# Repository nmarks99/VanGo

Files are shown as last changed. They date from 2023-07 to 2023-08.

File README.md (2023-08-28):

# VanGo: A Drawing Robot
VanGo is a differential drive robot that can draw SVG images on a page.

<p float="left">
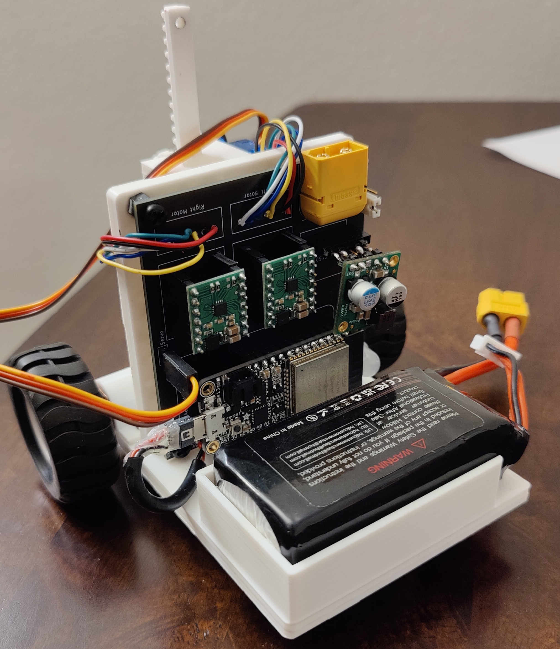
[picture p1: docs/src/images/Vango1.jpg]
  
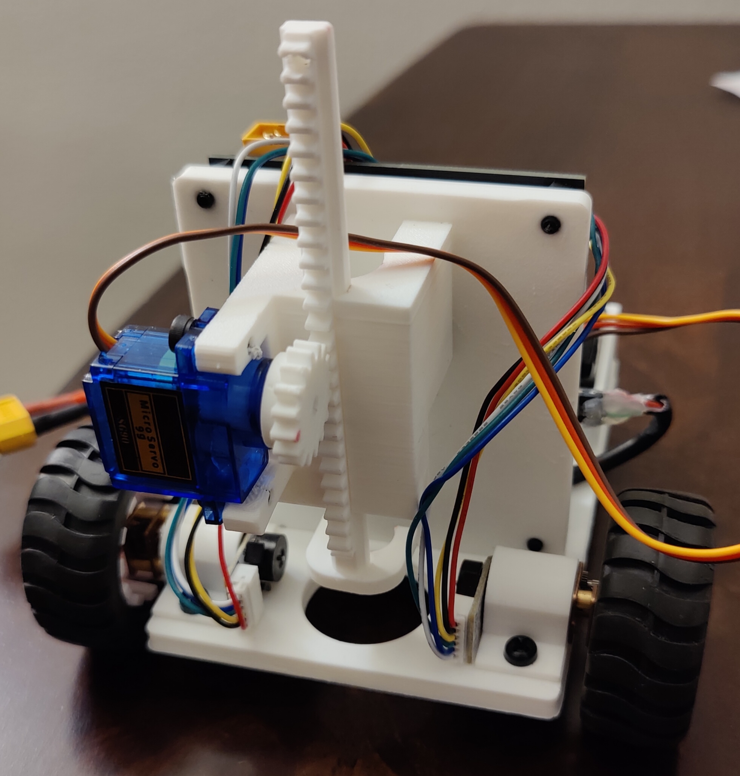
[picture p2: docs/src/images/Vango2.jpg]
   
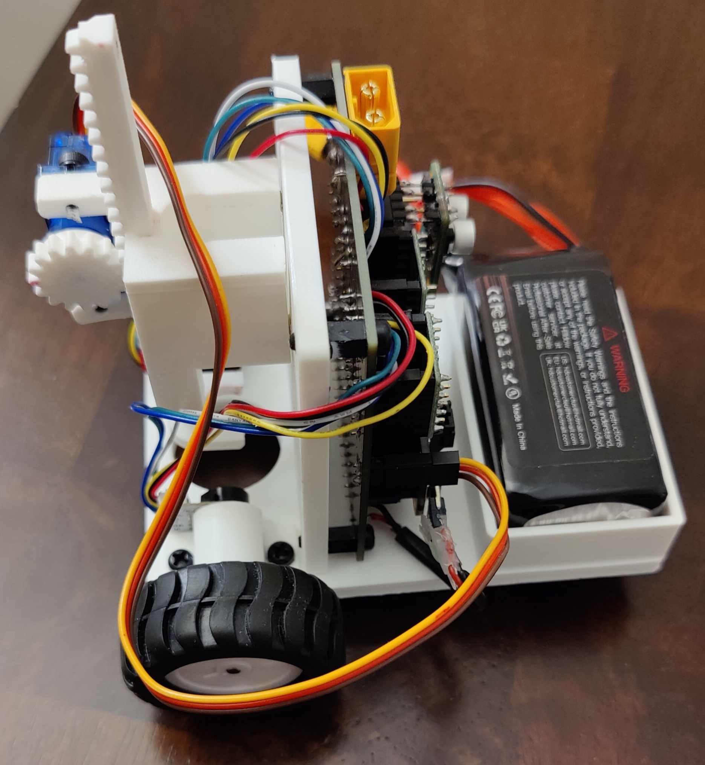
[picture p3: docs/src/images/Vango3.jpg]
  
</p>

First, an SVG image is converted to XY coordinates using this online tool: [Coordinator](https://spotify.github.io/coordinator/).
Then, using these XY coordinates, a trajectory of waypoints is generated for the robot to follow.
Trajectory tracking is implemented using a simple PID steering control algorithm, and the robot determines its pose in space
through wheel odometry, using quadrature encoders on the motors. For more in-depth information, please see the VanGo documentation
at [https://nmarks99.github.io/VanGo/](https://nmarks99.github.io/VanGo/). VanGo is still relatively early in development
and several aspects of the project need more work and fine tuning, such as the trajectory tracking algorithm, a command line interface
for the client application, and improved mechanical design. However, in its current state, VanGo demonstrates a good proof of concept.

## Project Structure
- `vango-firmware` is the firmware for the ESP32 board based on [esp-idf-hal](https://github.com/esp-rs/esp-idf-hal)
- `vango-client` is a desktop command line application for controlling the robot
- `vango-utils` is a utility library used by both the firmware and client.
- `hardware` directory contains the KiCAD project for the PCB

## Future Development
This project also uses another library I have developed, [diff-drive](https://github.com/nmarks99/diff-drive),
primarily for pose estimation via wheel odometry. In the future I hope to use both the VanGo and diff-drive projects
as starting points for developing a general purpose, high-performance, and open-source, differential drive robot
that anyone can build with firmware based on Rust on the ESP32 (think DIY [TurtleBot](https://www.robotis.us/turtlebot-3/)).

## Other Notes
One of my biggest motivations for this project was to learn more rust programming, particularly embedded rust, which is why
this project is 100% rust code 🦀. Like mostly everyone else, I've primarily used C and C++ for programming microcontrollers
in the past, most of the time using the Arduino framework together with PlatformIO which I've found to be a very pleasant
experience. After having worked on this project for several months, using Rust on the ESP32, I've found it to be a
equally pleasant experience, after some intial growing pains. Below are some of my opinions on the state of embedded Rust.
Note this is generally with regards to Rust on ESP [(esp-rs)](https://github.com/esp-rs), however some of it applies to embedded
Rust in a broader sense.

**The Good**
- Using `esp-idf-hal` you get to program the ESP32 in Rust (almost) as if you were writing a program on your desktop
This means you get to take full advantage of the Rust standard library and mostly any external crates you may need.
- Using Cargo works the same as it would in your other Rust projects and integrates seamlessly with flashing the board.
you can see in my vango-firmware/.cargo/config.toml file, I created an alias `cargo flash` to flash the board from the
command line and also set the partition table (sets how much space in memory you are reserving for your program):
`flash = "espflash --release --partition-table partitions.csv"`
- As in the case for non-embedded Rust, if the code compiles it almost always just works, which is super nice, especially
for embedded projects where you not only have to build, but also flash the board. I've found that bugs are often very easy
to track down in Rust. The only subtle error I encountered, and it's not even that subtle, is that if you accidentally
enter a loop that is doing nothing but looping, it will probably trigger the watchdog timer and continually reset the board.
There is a way to disable the WDT, but you can also just add a short delay (1ms even is enough) if you are in a loop doing
nothing.

**The Bad**
- Finding example code is (unsurpisingly since Arduino is much more mature) a little difficult compared to Arduino.
For example, I had a very tough time finding an example of how to do some basic things like GPIO interrpts
and timer based interrupts, which I could find examples for very easily in Arduino. However, after figuring it out,
a timer interrupt in `esp-idf-hal` turns out to be almost as easy to use as the popular [IntervalTimer](https://www.pjrc.com/teensy/td_timing_IntervalTimer.html)
in Arduino. Another thing that was very tough to find example code for was bluetooth. Eventually I found [esp32-nimble](https://github.com/taks/esp32-nimble)
which works quite well and isn't too complicated. The developer is was also quick to reply to an issue I opened for an additional feature.
- Flashing the board takes *forever*. I haven't timed it but it probably takes like a minute or two maybe which is much longer than similar Arduino
programs. This may just be something specific to my project, but it was fairly annoying to wait for the board to be flashed whenever I made updates.

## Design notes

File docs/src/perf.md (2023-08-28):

# Performance
In its current stage, the VanGo drawing robot does not work well enough to draw
consistent and accurace images, however with additional tuning, a more sophisticated
trajectory tracking algorithm, and possibly additional sensors, the performance will
improve. Manual mode, which enables a user to manually drive the robot and move
the marker up and down works as desired. Below the results of several tests are shown.

## Test 1: Manual Mode "Hi"
In the video linked below, I manually controlled the robot using the `vango-client`
application to write "Hi". This worked fairly well, but as you can see, driving the robot
smoothly with the current controls is a bit challenging.

[Test 1 Video](https://drive.google.com/file/d/1G3J-nfXMaDWAlqaTBmTTMUwiaXZAd-wS/view?usp=sharing)

## Test 2: Automatic Mode "Triangle"
The video linked below performs a test of the robot in automatically mode
attempting to draw a triangle. There is also a plot of the estimated x and y
position of the robot from wheel odometry. As you can see the actual position
of the robot is not very good, however the position estimate from odometry appears to be
a bit better. This could potentially be due to wheel slipping.

[Test 2 Video](https://drive.google.com/file/d/1G4sDGH2qyjXhTE3TqAN95uGIOtFKYngA/view?usp=drive_link)

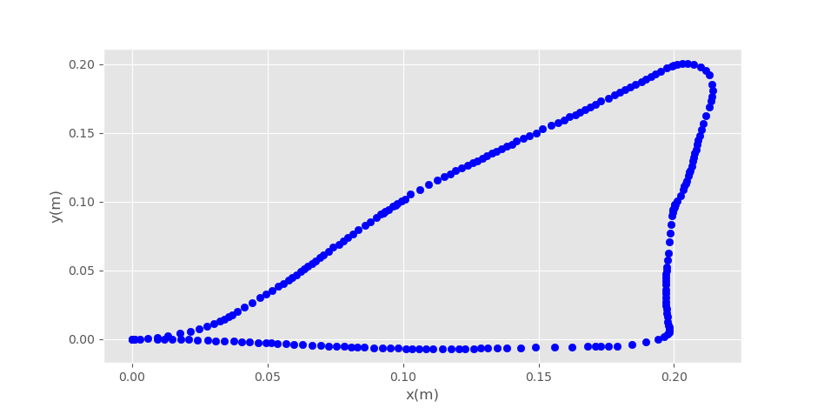
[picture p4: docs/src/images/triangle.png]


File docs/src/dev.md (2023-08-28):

# Embedded Development
To set up a development environment to modify and flash firmware to the device,
you will need to install several things such as the Espressif compiler toolchain,
espflash cargo utility, and of course rust and cargo if you don't have that already.

The best way to get all this setup and make sure it works is to follow the directions
on setting up an `esp-idf-template` project: [esp-idf-template](https://github.com/esp-rs/esp-idf-template).
If you are able to successfully build the template project, you should in theory be able to build and flash
the `vango-firmware` without issue. In the `vango-firmware/.cargo/config.toml` file, there is an alias
for "flash", which allows you to flash the board with `espflash` by simply typing `cargo flash`.

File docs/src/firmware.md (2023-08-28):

# Firmware
The firmware running on the ESP32 microcontroller is contained in the `vango-firmware` directory.
The firmware is responsible for establishing Bluetooth Low-Energy (BLE) communications,
reading encoders, computing wheel angles and speeds,and computing the robot's pose through wheel odometry.

## Communication
The VanGo robot is controlled via a BLE server. Using the `esp32-nimble` crate with `esp-idf-hal`,
several BLE characteristics are established. For those unfamiliar with BLE, a characteristic is simply
a part of the server that a client can read/write data to. Each characteristic is given a
unique UUID to identify it by.

Below are the BLE characteristics provided by the robot and some information about what they are for.

**Left/Right Speed Characteristics** (Read | Write):
- Read: When read from, returns the current wheel speed
- Write: When written to, sets the target wheel speed to the written value

**Pose X, Y, and \\(\theta\\) Characteristics** (Read | Write):
- Read: When read from, returns the current x,y, or \\(\theta\\) position of the robot
- Write: When '0' is written to these characteristics, the value is zeroed

**Pen Characteristic** (WRITE):
- Write: When '1' is written, raises the pen, when '0' is written, lowers the pen

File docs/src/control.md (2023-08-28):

# Control
VanGo's control architecture is comprised of a lower level speed control loop
and a higher level trajectory tracking controller. From a user perspective, the lower level
control loop can mostly be ignored, or at least treated as a black box and not modified, while the
higher level controller may leave more room for customization.

## Low-Level Speed Controller
Running on the ESP32 microcontroller, a timer based interrupt is resposible for reading the
quadrature wheel encoders to compute the speed of the wheels. Experimentally it was determined that
a simply proportional controller was sufficient for closed-loop speed control, although Proportional-Derivative (PD)
control was also tested. Although PD control results is a smoother trajectory with less overshoot, the slower response
was not worth the minimization of overshoot. Either way, both P and PD controllers work fairly well for closed-loop
speed control, and if one is preferred by the user, the gains may be adjusted in the firmware and reflashed to the board.
For more information on editing and flashing firmware, see [Development](./dev.md).

The two images below show the speed controller response for both the Proportional and Proportional-Derivative controllers.
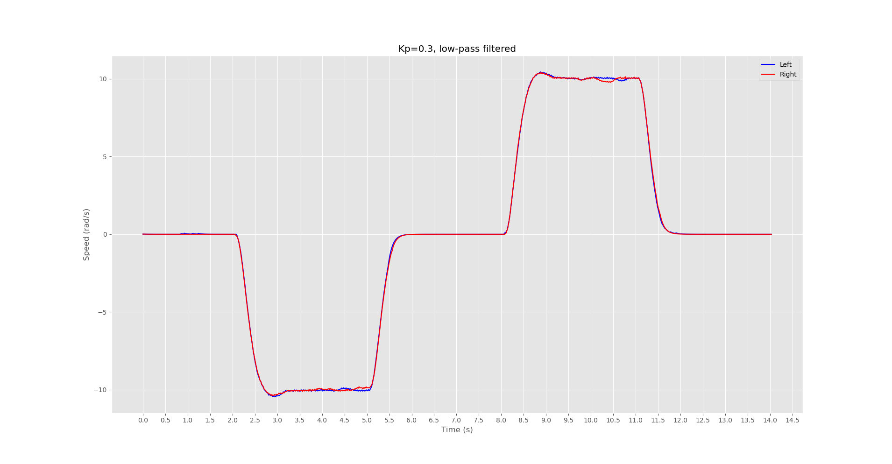
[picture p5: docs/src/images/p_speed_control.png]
Proportional control


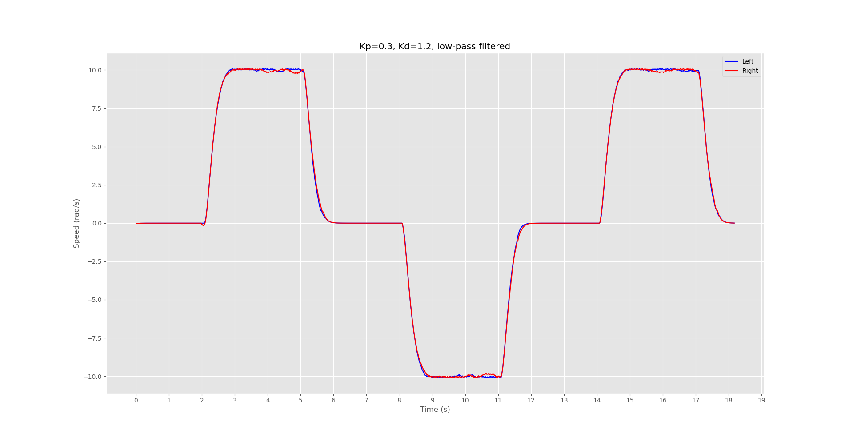
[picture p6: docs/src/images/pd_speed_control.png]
Proportional-Derivative control


## High-Level Trajectory Controller
The `vango-client` implements a trajectory tracking algorithm which is used to follow a trajectory defined
by a set of waypoints.

There are many different trajectory tracking algorithms in existance, however at this time only one,and perhaps the most basic one,the PID controller, has been implemented for the VanGo robot. There are various ways a PID controller can be applied to the trajectory tracking problem, however the method I've chosen to implement is to use a PID controller for angular velocity control. To move the robot from its current (x, y) to some goal position which is presumably along the target path, the algorithm works as follows:
1. Read the current pose (computed from wheel odometry) via BLE
2. Compute the target angle as \\(atan2(y_{goal} - y, x_{goal} - x)\\)
3. Let the error be the minimum angle between the robots current heading and the target heading
4. Compute the control signal from the PID controller for the given error. This control signal is chosen to represent the angular velocity of the robot.
5. The desired motion of the robot is then represented as a 2D twist (body velocity), using the computed target angular velocity, a constant x velocity of your choice, and a y velocity of 0.0 (which assumes no wheel slipping)
6. Compute the left and right wheel speeds needed to achieve the target twist

During development, there was a choice to be made regarding whether the trajectory controller
will operate at the client application level or the firmware level. Both options have positives and negatives and will be briefly discussed below. In the end, it was chosen to operate the trajectory controller at the client application level.

### Client-Side Trajectory Controller
A client side trajectory controller works by implementing the trajectory tracking algorithm in the `vango-client`
application. The controller will obtain the robots current pose using bluetooth low-energy (BLE) and compute the necessary wheel speeds for tracking the desired trajectory, and send those target wheel
speeds back to the robot over BLE.

**Pros**
- Faster development time since you will not need to reflash the microcontroller
- Easier to test different trajectory tracking algorithms or enable several algorithms to be available as options to the user
- Can take advantage of a client machine with higher computing power than the microcontroller

**Cons**
- Control loop speed is limited by BLE read/write latency. In it's current state, loop speeds top out around 30Hz.

### Firmware-Side Trajectory Controller
An alternative way to implement the trajectory tracking controller would be to implement the controller in the firmware on the microcontroller, obtaining the target path to follow from the client over BLE. Pros and Cons are listed below.

**Pros**
- The MCU is capable of more precise and consistant timing through the use of hardware timers and interrupts
- BLE communication latency is no longer a concern since waypoints could be sent and processed beforehand

**Cons**
- Resources are somewhat limited on the MCU and may impose practical limits of which algorithms can be employed
- Slower development time since for the most part, modifications to the trajectory tacking algorithm require reflashing the board

Although performance/timing of the control loop could potentially be better if implemented in the MCU, it was determined that easy customization of algorithms as well as development time are key aspects of the project, therefore a client-side trajectory tracking algorithm was employed.

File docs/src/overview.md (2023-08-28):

# Overview

<p float="left">
  
   
  
</p>

VanGo is a differential drive robot for drawing SVG images. Put simply,
VanGo is a wheeled mobile robot capable of trajectory tracking,
with the added feature that the trajectory is generated from an SVG
image and the robot holds a marker which is brought into contact with the
page while the robot is on the desired path, thus drawing the SVG image.

## Usage
A basic explanation of how VanGo is used and what goes on under-the-hood during general use is explained below.
More in-depth explaination can be found is later sections of this site.
1. The user produces a CSV file containing (x,y) points from a SVG image using [Coordinator](spotify.github.io/coordinator)
2. The user starts the `vango-client` program, providing the CSV file
3. A path of waypoints is generated from the CSV file and clustered into closed curves based on some threshold distance
4. The robot will navigate to the first point in the next closed curve
5. Lower the marker, then navigate to each additional point in the same closed curve
6. After passing through all the points in this closed curve, raise the marker and go back to step 4.

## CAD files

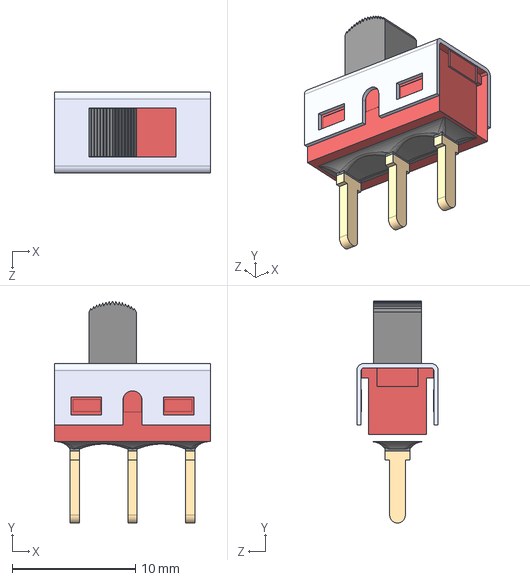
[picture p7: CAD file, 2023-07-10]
hardware/vango-pcb/500SSP1S1M2REA/500SSP1S1M2REA.step
12.7 x 18.0 x 6.60 mm

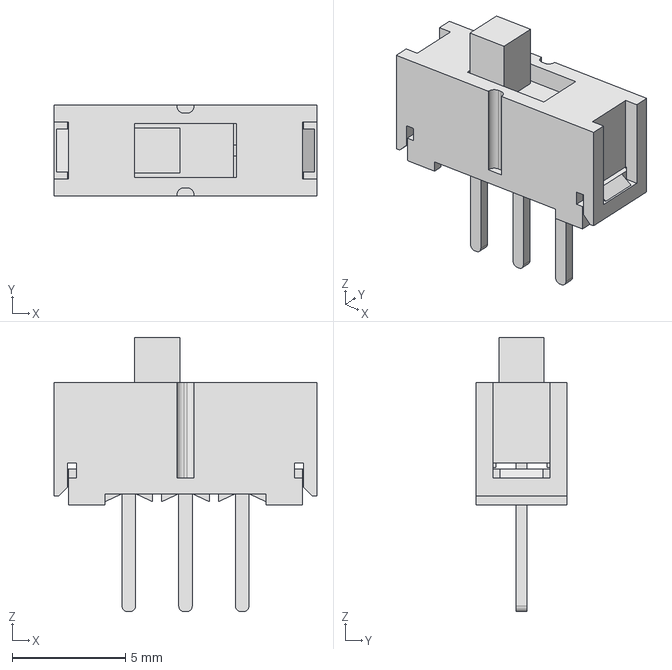
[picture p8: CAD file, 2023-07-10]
hardware/vango-pcb/EG1218_switch/EG1218.step
11.6 x 4.00 x 12.1 mm

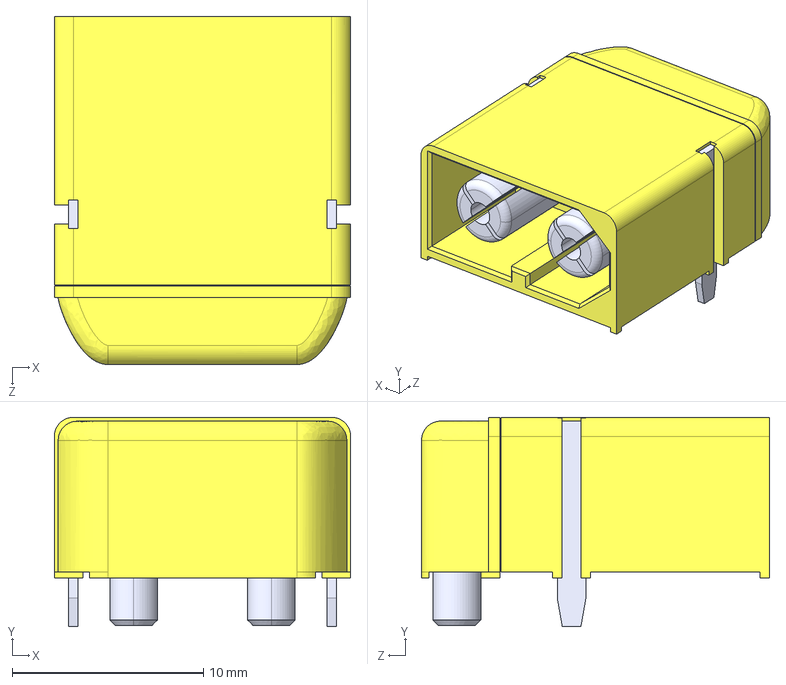
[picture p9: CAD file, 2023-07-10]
hardware/vango-pcb/XT60/XT60PW-M.step
15.5 x 11.0 x 18.2 mm

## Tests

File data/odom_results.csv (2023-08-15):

time(ms) | left_angle(rad) | right_angle(rad) | theta(rad) | x(m) | y(m)
25 | 0.00448799 | 0.00448799 | 0 | 0.00010097978 | 0
45 | 0.00448799 | 0.01795196 | 0.0029411586 | 0.00025244924 | 0.00000022178463
65 | 0.01795196 | 0.03141593 | 0.0029411586 | 0.00055538764 | 0.0000009642778
85 | 0.0448799 | 0.053855877 | 0.0019607726 | 0.001110775 | 0.0000021779802
105 | 0.07180784 | 0.080783814 | 0.0019607726 | 0.0017166525 | 0.0000033659696
125 | 0.107711755 | 0.11668773 | 0.0019607726 | 0.002524489 | 0.0000049499554
145 | 0.14810365 | 0.16605562 | 0.003921547 | 0.003534282 | 0.000007965572
165 | 0.20195954 | 0.22439949 | 0.00490193 | 0.0047965157 | 0.000013878634
185 | 0.2692794 | 0.2962073 | 0.0058823167 | 0.006361677 | 0.000022711372
205 | 0.3455752 | 0.36801517 | 0.00490193 | 0.008027817 | 0.00003209477
225 | 0.435335 | 0.45777494 | 0.00490193 | 0.010047388 | 0.000041994645
245 | 0.5340708 | 0.55651075 | 0.00490193 | 0.012268917 | 0.000052884512
265 | 0.63280654 | 0.6552465 | 0.00490193 | 0.014490445 | 0.00006377437
285 | 0.74051833 | 0.75847024 | 0.0039215307 | 0.016863443 | 0.000074841926
305 | 0.85720605 | 0.87067 | 0.0029411572 | 0.019438405 | 0.00008556373
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

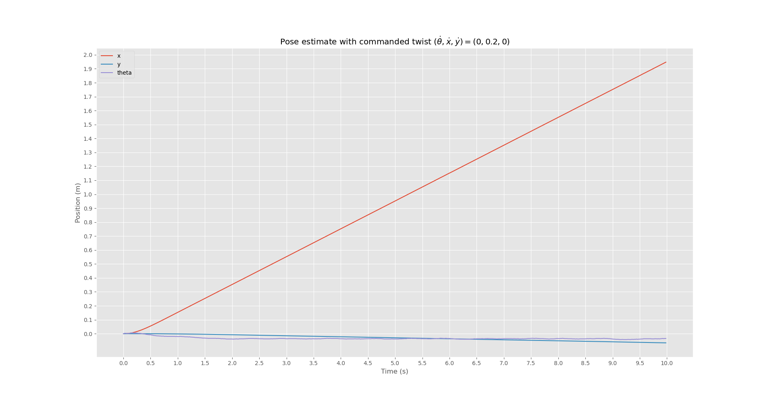
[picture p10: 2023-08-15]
docs/book/images/odom_results.png

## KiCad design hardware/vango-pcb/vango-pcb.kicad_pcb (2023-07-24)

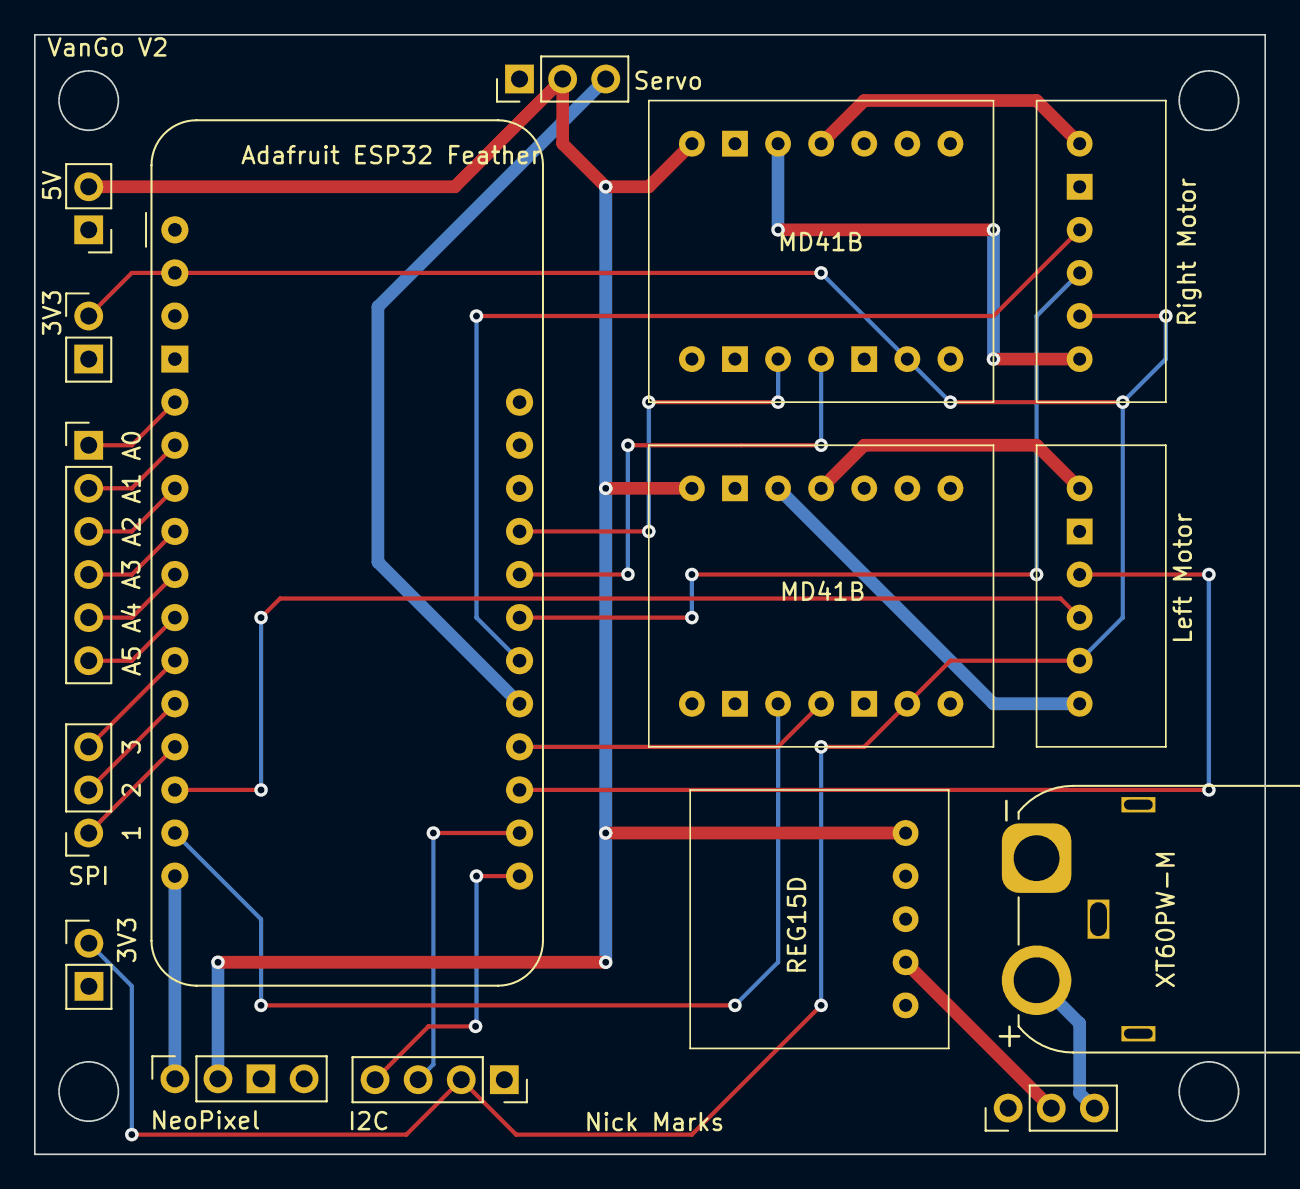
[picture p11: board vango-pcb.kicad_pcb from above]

Board: 2 copper layers, 72.5 x 66.0 mm, 16 parts (0 on the bottom side), 30 nets.

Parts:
3V3: Conn_01x02; PinHeader_1x02_P2.54mm_Vertical
A1: Adafruit_Feather_HUZZAH32_ESP32; Adafruit_Feather
J1: XT60PW-M; AMASS_XT60IPW-M_1x03_P7.20mm_Horizontal
J2: NeoPixel; PinSocket_1x04_P2.54mm_Vertical
J3: I2C; PinSocket_1x04_P2.54mm_Vertical
J4: Conn_01x06; PinHeader_1x06_P2.54mm_Vertical
J5: SPI; PinSocket_1x03_P2.54mm_Vertical
J6, J7: Conn_01x02; PinHeader_1x02_P2.54mm_Vertical
SW1: SW_SPDT; PinHeader_1x03_P2.54mm_Vertical
Servo: SG90_Servo; PinHeader_1x03_P2.54mm_Vertical
U1, U3: MD41B
U2: REG15D
U4: Left Motor; N20_motor
U5: Right Motor; N20_motor

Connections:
+3V3: 3V3.1, A1.2 (3V3), J3.2, J6.1, U1.6 (~SLEEP), U3.6 (~SLEEP), U4.5 (VCC), U5.5 (VCC)
+5V: J2.2, J7.2, Servo.2, U1.8 (VIN), U2.5 (VOUT), U3.8 (VIN)
/A0: A1.5 (DAC2/A0), J4.1
/A1: A1.6 (DAC1/A1), J4.2
/A2: A1.7 (I34/A2), J4.3
/A3: A1.8 (I39/A3), J4.4
/A4: A1.9 (IO36/A4), J4.5
/A5: A1.10 (IO4/A5), J4.6
/A8: A1.21 (A8/IO15), Servo.3
/IO12: A1.24 (A11/IO12), U3.4 (PH/IN2)
/IO13: A1.25 (A12/IO13), U3.3 (EN/IN1)
/IO14: A1.19 (A6/IO14), U4.3 (C1)
/IO16: A1.14 (RX/IO16), U4.4 (C2)
/IO17: A1.15 (TX/IO17), U1.3 (EN/IN1)
/IO27: A1.23 (A10/IO27), U5.4 (C2)
/IO32: A1.20 (A7/IO32), U1.4 (PH/IN2)
/IO33: A1.22 (A9/IO33), U5.3 (C1)
/MISO: A1.13 (MISO/IO19), J5.1
/MOSI: A1.12 (MOSI/IO18), J5.2
/SCK: A1.11 (SCK/IO5), J5.3
/SCL: A1.18 (SCL/IO22), J3.3
/SDA: A1.17 (SDA/IO23), J3.4
GND: 3V3.2, A1.4 (GND), J1.1 (-), J2.3, J3.1, J6.2, J7.1, Servo.1, U1.2 (GND), U1.5 (PMODE), U1.9 (GND), U2.3 (GND), U2.4 (GND), U3.2 (GND), U3.5 (PMODE), U3.9 (GND), U4.2 (GND), U5.2 (GND)
unnamed: A1.16 (IO21), J2.1
unnamed: J1.2 (+), SW1.3 (C)
unnamed: SW1.2 (B), U2.2 (VIN)
unnamed: U1.10 (OUT1), U4.6 (M2)
unnamed: U1.11 (OUT2), U4.1 (M1)
unnamed: U3.10 (OUT1), U5.6 (M2)
unnamed: U3.11 (OUT2), U5.1 (M1)

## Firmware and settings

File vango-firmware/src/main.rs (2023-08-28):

// Basics
use atomic_float::AtomicF32;
use core::sync::atomic::{AtomicBool, AtomicI32, Ordering};
use core::time::Duration;
use esp_idf_hal::delay::FreeRtos;
use esp_idf_hal::peripherals::Peripherals;
use esp_idf_hal::prelude::*;
use esp_idf_sys as _;

// GPIO
use esp_idf_hal::gpio::PinDriver;

// LEDC (PWM)
use esp_idf_hal::ledc::config::TimerConfig;
use esp_idf_hal::ledc::LedcDriver;
use esp_idf_hal::ledc::LedcTimerDriver;

// TIME
use esp_idf_hal::task::executor::{FreeRtosMonitor, Monitor, Notify};
use esp_idf_svc::systime::EspSystemTime;
static SYS_TIMER: EspSystemTime = EspSystemTime {};

// BLE
use esp32_nimble::utilities::BleUuid;
use esp32_nimble::{uuid128, BLEDevice, NimbleProperties};

// diff-drive
use diff_drive::ddrive::{DiffDrive, WheelState};
use diff_drive::rigid2d::Pose2D;

// local modules
mod encoder;
mod neopixel;
mod pen;
use encoder::Encoder;
use encoder::{ENCODER_RATE_MS, TICKS_PER_RAD};
use neopixel::{Color, Neopixel};
use pen::Pen;
use vango_utils as utils;

// Atomic variables
static LEFT_COUNT: AtomicI32 = AtomicI32::new(0);
static RIGHT_COUNT: AtomicI32 = AtomicI32::new(0);
static LEFT_SPEED: AtomicF32 = AtomicF32::new(0.0);
static LEFT_ANGLE: AtomicF32 = AtomicF32::new(0.0);
static RIGHT_ANGLE: AtomicF32 = AtomicF32::new(0.0);
static RIGHT_SPEED: AtomicF32 = AtomicF32::new(0.0);
static LEFT_DUTY: AtomicF32 = AtomicF32::new(0.0);
static RIGHT_DUTY: AtomicF32 = AtomicF32::new(0.0);
static ISR_FLAG: AtomicBool = AtomicBool::new(false);
static TARGET_SPEED_LEFT: AtomicF32 = AtomicF32::new(0.0);
static TARGET_SPEED_RIGHT: AtomicF32 = AtomicF32::new(0.0);
static POSE_X: AtomicF32 = AtomicF32::new(0.0);
static POSE_Y: AtomicF32 = AtomicF32::new(0.0);
static POSE_THETA: AtomicF32 = AtomicF32::new(0.0);

// BLE UUIDs
const VANGO_SERVICE_UUID: BleUuid = uuid128!("21470560-232e-11ee-be56-0242ac120002");
const LEFT_SPEED_UUID: BleUuid = uuid128!("3c9a3f00-8ed3-4bdf-8a39-a01bebede295");
const RIGHT_SPEED_UUID: BleUuid = uuid128!("c0ffc89c-29bb-11ee-be56-0242ac120002");
const WAYPOINT_UUID: BleUuid = uuid128!("21e16dea-357a-11ee-be56-0242ac120002");
const POSE_THETA_UUID: BleUuid = uuid128!("3cedc40e-3655-11ee-be56-0242ac120002");
const POSE_X_UUID: BleUuid = uuid128!("a0c2b3b2-3b1a-11ee-be56-0242ac120002");
const POSE_Y_UUID: BleUuid = uuid128!("a0c2b65a-3b1a-11ee-be56-0242ac120002");
const PEN_UUID: BleUuid = uuid128!("0daaac7c-3d6a-11ee-be56-0242ac120002");

// Speed controller
// Proportional control seems fine and is faster
const KP: f32 = 0.3;
const KD: f32 = 0.0;
const DIR_CHANGE_THRESHOLD: f32 = 1.0;

// Robot paramaters
const WHEEL_RADIUS: f32 = 0.045 / 2.0; // meters
const WHEEL_SEPARATION: f32 = 0.105; // meters

fn main() -> anyhow::Result<()> {
    esp_idf_sys::link_patches();
    let peripherals = Peripherals::take().unwrap();
    esp_idf_svc::log::EspLogger::initialize_default();

    // Set up neopixel
    let mut neo = Neopixel::new(peripherals.pins.gpio21, peripherals.rmt.channel0)?;
    neo.set_color(Color::Purple, 0.2)?;

    // Set up Pen
    let mut pen = Pen::new(
        peripherals.pins.gpio15,
        peripherals.ledc.channel2,
        peripherals.ledc.timer2,
    )?;
    pen.up()?;

    // Set up BLE server
    let ble_device = BLEDevice::take();
    let server = ble_device.get_server();
    server.on_connect(|server, desc| {
        log::info!("Client connected");
        ble_device.get_advertising().start().unwrap();
        server
            .update_conn_params(desc.conn_handle, 6, 12, 0, 60)
            .unwrap()
    });
    let ble_service = server.create_service(VANGO_SERVICE_UUID);

    // BLE characteristic for waypoints
    let waypoint_blec = ble_service
        .lock()
        .create_characteristic(WAYPOINT_UUID, NimbleProperties::WRITE);
    waypoint_blec.lock().on_write(move |recv| {
        let waypoint_bytes = recv.recv_data;
        log::info!("Waypoint: {:?}", waypoint_bytes);
    });

    // BLE characteristic for setting the pen up/down
    let pen_blec = ble_service
        .lock()
        .create_characteristic(PEN_UUID, NimbleProperties::WRITE | NimbleProperties::READ);
    pen_blec.lock().on_write(move |recv| {
        let v = recv.recv_data;
        if v.len() == 1 {
            match v[0] {
                b'1' => {
                    let _ = pen.up();
                }
                b'0' => {
                    let _ = pen.down();
                }
                _ => log::error!("Invalid input: '{}' to pen ble characteristic ", v[0]),
            };
        } else {
            log::error!(
                "Invalid number of values sent to pen characteristic, expected 1, received {}",
                v.len()
            );
        }
    });

    // BLE characteristics for pose estimate from odometry
    let pose_x_blec = ble_service
        .lock()
        .create_characteristic(POSE_X_UUID, NimbleProperties::READ);
    pose_x_blec.lock().on_read(move |v, _| {
        let pose_x = POSE_X.load(Ordering::Acquire);
        v.set_value(&utils::f32_to_ascii(pose_x));
    });
    let pose_y_blec = ble_service
        .lock()
        .create_characteristic(POSE_Y_UUID, NimbleProperties::READ);
    pose_y_blec.lock().on_read(move |v, _| {
        let pose_y = POSE_Y.load(Ordering::Acquire);
        v.set_value(&utils::f32_to_ascii(pose_y));
    });
    let pose_theta_blec = ble_service
        .lock()
        .create_characteristic(POSE_THETA_UUID, NimbleProperties::READ);
    pose_theta_blec.lock().on_read(move |v, _| {
        let pose_theta = POSE_THETA.load(Ordering::Acquire);
        v.set_value(&utils::f32_to_ascii(pose_theta));
    });

    // BLE characteristic for left motor speed
    let left_speed_blec = ble_service.lock().create_characteristic(
        LEFT_SPEED_UUID,
        NimbleProperties::READ | NimbleProperties::WRITE,
    );
    left_speed_blec
        .lock()
        .on_read(move |v, _| {
            let speed = LEFT_SPEED.load(Ordering::Acquire);
            v.set_value(&utils::f32_to_ascii(speed));
        })
        .on_write(move |recv| {
            let target_recv: f32 = utils::ascii_to_f32(recv.recv_data.to_vec()).unwrap();
            TARGET_SPEED_LEFT.store(target_recv, Ordering::Release);
        });

    // BLE characteristic for right motor speed
    let right_speed_blec = ble_service.lock().create_characteristic(
        RIGHT_SPEED_UUID,
        NimbleProperties::READ | NimbleProperties::WRITE,
    );
    right_speed_blec
        .lock()
        .on_read(move |v, _| {
            let speed = RIGHT_SPEED.load(Ordering::Acquire);
            v.set_value(&utils::f32_to_ascii(speed));
        })
        .on_write(move |recv| {
            let target_recv: f32 = utils::ascii_to_f32(recv.recv_data.to_vec()).unwrap();
            TARGET_SPEED_RIGHT.store(target_recv, Ordering::Release);
        });

    // start BLE advertising
    let ble_advertising = ble_device.get_advertising();
    ble_advertising
        .name("VanGo")
        .add_service_uuid(VANGO_SERVICE_UUID);
    ble_advertising.start().unwrap();

    // configure PWM on GPIO15 for motor 1
    let mut left_pwm_driver = LedcDriver::new(
        peripherals.ledc.channel0,
        LedcTimerDriver::new(
            peripherals.ledc.timer0,
            &TimerConfig::new().frequency(80.Hz().into()),
        )?,
        peripherals.pins.gpio13,
    )?;

    // configure PWM on GPIO23 for motor 2
    let mut right_pwm_driver = LedcDriver::new(
        peripherals.ledc.channel1,
        LedcTimerDriver::new(
            peripherals.ledc.timer1,
            &TimerConfig::new().frequency(80.Hz().into()),
        )?,
        peripherals.pins.gpio17,
    )?;

    // Set initial motor directions to forward
    let mut left_direction = PinDriver::output(peripherals.pins.gpio12)?;
    let mut right_direction = PinDriver::output(peripherals.pins.gpio32)?;
    left_direction.set_low()?;
    right_direction.set_high()?;
    let max_duty = right_pwm_driver.get_max_duty();

    // set up encoder for each motor
    let left_encoder = Encoder::new(
        peripherals.pcnt0,
        peripherals.pins.gpio27,
        peripherals.pins.gpio33,
    )?;
    let right_encoder = Encoder::new(
        peripherals.pcnt1,
        peripherals.pins.gpio14,
        peripherals.pins.gpio16,
    )?;

    // Make a task (timer interrupt) for computing motor speed
    let task_timer = esp_idf_svc::timer::EspTaskTimerService::new().unwrap();
    let monitor = FreeRtosMonitor::new();
    let monitor_notify = monitor.notifier();

    const ALPHA: f32 = 0.1; // used in low-pass filter
    let mut left_speed_smooth = 0.0;
    let mut right_speed_smooth = 0.0;
    let mut left_err_last = 0.0;
    let mut right_err_last = 0.0;

    // Timer based ISR
    let task_timer = task_timer
        .timer(move || {
            monitor_notify.notify(); // not sure what this does
            ISR_FLAG.store(true, Ordering::SeqCst);

            // Get counts and fix angle
            let left_count = -left_encoder.get_value().unwrap() as i32;
            let right_count = -right_encoder.get_value().unwrap() as i32;

            // Compute angles
            let left_angle = left_count as f32 / TICKS_PER_RAD;
            let right_angle = right_count as f32 / TICKS_PER_RAD;

            // Compute speeds
            let left_count_last = LEFT_COUNT.load(Ordering::SeqCst);
            let mut left_speed = (left_count as f32 - left_count_last as f32)
                / (TICKS_PER_RAD * ENCODER_RATE_MS as f32 / 1000.0);
            let right_count_last = RIGHT_COUNT.load(Ordering::SeqCst);
            let mut right_speed = (right_count as f32 - right_count_last as f32)
                / (TICKS_PER_RAD * ENCODER_RATE_MS as f32 / 1000.0);

            // Low-pass filter the speed to remove high frequency noise
            left_speed_smooth = ALPHA * left_speed + (1.0 - ALPHA) * left_speed_smooth;
            right_speed_smooth = ALPHA * right_speed + (1.0 - ALPHA) * right_speed_smooth;
            left_speed = left_speed_smooth;
            right_speed = right_speed_smooth;

            // Store the counts, angles(rad), and speeds(rad/s)
            LEFT_COUNT.store(left_count, Ordering::SeqCst);
            RIGHT_COUNT.store(right_count, Ordering::SeqCst);
            LEFT_ANGLE.store(left_angle, Ordering::SeqCst);
            RIGHT_ANGLE.store(right_angle, Ordering::SeqCst);
            LEFT_SPEED.store(left_speed, Ordering::SeqCst);
            RIGHT_SPEED.store(right_speed, Ordering::SeqCst);

            // Load target speeds
            let mut target_speed_left = TARGET_SPEED_LEFT.load(Ordering::SeqCst);
            let mut target_speed_right = TARGET_SPEED_RIGHT.load(Ordering::SeqCst);

            // prevent abrupt direction changes
            // probably should just got immediately to zero then change direction
            if utils::opposite_signs(target_speed_left, left_speed)
                && left_speed.abs() > DIR_CHANGE_THRESHOLD
            {
                target_speed_left = if left_speed > 0.0 {
                    DIR_CHANGE_THRESHOLD
                } else {
                    -DIR_CHANGE_THRESHOLD
                };
            }
            if utils::opposite_signs(target_speed_right, right_speed)
                && right_speed.abs() > DIR_CHANGE_THRESHOLD
            {
                target_speed_right = if right_speed > 0.0 {
                    DIR_CHANGE_THRESHOLD
                } else {
                    -DIR_CHANGE_THRESHOLD
                };
            }

            // Compute the error and derivative error
            let err_left = target_speed_left - left_speed;
            let err_right = target_speed_right - right_speed;
            let drv_err_left = err_left - left_err_last;
            let drv_err_right = err_right - right_err_last;

            // Compute the control signal (PID controller)
            let mut u_left = KP * err_left + KD * drv_err_left;
            let mut u_right = KP * err_right + KD * drv_err_right;

            left_err_last = err_left;
            right_err_last = err_right;

            // Adjust control signal based on sign of target speed
            if target_speed_left < 0.0 {
                // Backward
                u_left = -u_left;
                let _ = left_direction.set_high();
            } else if target_speed_left > 0.0 {
                // Forward
                let _ = left_direction.set_low();
            } else {
                if left_speed > 0.0 {
                    let _ = left_direction.set_low();
                } else if left_speed < 0.0 {
                    u_left = -u_left;
                    let _ = left_direction.set_high();
                }
            }
            if target_speed_right < 0.0 {
                // Backward
                u_right = -u_right;
                let _ = right_direction.set_low();
            } else if target_speed_right > 0.0 {
                // Forward
                let _ = right_direction.set_high();
            } else {
                if right_speed > 0.0 {
                    let _ = right_direction.set_high();
                } else if right_speed < 0.0 {
                    u_right = -u_right;
                    let _ = right_direction.set_low();
                }
            }

            // load the last duty cycle value and compute new duty cycle
            let mut left_duty = LEFT_DUTY.load(Ordering::SeqCst);
            let mut right_duty = RIGHT_DUTY.load(Ordering::SeqCst);
            left_duty = left_duty + u_left;
            if left_duty > max_duty as f32 {
                left_duty = max_duty as f32;
            } else if left_duty < 0.0 {
                left_duty = 0.0;
            }
            right_duty = right_duty + u_right;
            if right_duty > max_duty as f32 {
                right_duty = max_duty as f32;
            } else if right_duty < 0.0 {
                right_duty = 0.0;
            }

            LEFT_DUTY.store(left_duty, Ordering::SeqCst);
            RIGHT_DUTY.store(right_duty, Ordering::SeqCst);

            // Set the motor to this duty cycle
            if target_speed_left.abs() > DIR_CHANGE_THRESHOLD {
                let _ = left_pwm_driver.set_duty(left_duty as u32);
            } else {
                let _ = left_pwm_driver.set_duty(0u32);
            }
            if target_speed_right.abs() > DIR_CHANGE_THRESHOLD {
                let _ = right_pwm_driver.set_duty(right_duty as u32);
            } else {
                let _ = right_pwm_driver.set_duty(0u32);
            }
        })
        .unwrap();
    task_timer
        .every(Duration::from_millis(ENCODER_RATE_MS))
        .unwrap();

    let mut robot = DiffDrive::new(WHEEL_RADIUS, WHEEL_SEPARATION);
    let colors = vec![
        Color::Red,
        Color::Blue,
        Color::Green,
        Color::Yellow,
        Color::Purple,
        Color::Cyan,
        Color::White,
    ];
    let mut color_index: usize = 0;
    let mut count = 0;

    loop {
        // If the values have been updated, compute the pose from odometry
        let isr_flag = ISR_FLAG.load(Ordering::Relaxed);
        if isr_flag {
            // Get current wheel angles and compute pose
            let wheel_angles = WheelState::new(
                LEFT_ANGLE.load(Ordering::Relaxed),
                RIGHT_ANGLE.load(Ordering::Relaxed),
            );
            let pose = robot.forward_kinematics(wheel_angles);

            POSE_X.store(pose.x, Ordering::Relaxed);
            POSE_Y.store(pose.y, Ordering::Relaxed);
            POSE_THETA.store(pose.theta, Ordering::Relaxed);
            ISR_FLAG.store(false, Ordering::Relaxed);

            if count > 10 {
                neo.set_color(colors[color_index], 0.2)?;
                if color_index < colors.len() - 1 {
                    color_index += 1;
                } else {
                    color_index = 0;
                }
                count = 0;
            } else {
                count += 1;
            }
        } else {
            FreeRtos::delay_ms(1); // prevents WDT triggering
        }
    }
}

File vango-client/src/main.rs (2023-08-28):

#![allow(dead_code)]
use std::error::Error;

use bluest::{Adapter, Uuid};
use futures_util::StreamExt;
// use std::time::Duration;
use tracing::info;
use tracing::metadata::LevelFilter;

use std::io::Write;
use termion::event::Key;
use termion::input::TermRead;
use termion::raw::IntoRawMode;

mod cluster;
use diff_drive::ddrive::{DiffDrive, WheelState};
use diff_drive::rigid2d::{Pose2D, Twist2D, Vector2D};
use diff_drive::trajectory::Path;
use diff_drive::utils::{normalize_angle, rad2deg};
use vango_utils as utils;
use vango_utils::{almost_equal, ascii_to_f32, f32_to_ascii, get_min_angle};

const VANGO_SERVICE_ID: Uuid = Uuid::from_u128(0x21470560_232e_11ee_be56_0242ac120002);
const LEFT_SPEED_UUID: Uuid = Uuid::from_u128(0x3c9a3f00_8ed3_4bdf_8a39_a01bebede295);
const RIGHT_SPEED_UUID: Uuid = Uuid::from_u128(0xc0ffc89c_29bb_11ee_be56_0242ac120002);
const LEFT_COUNTS_UUID: Uuid = Uuid::from_u128(0x0a286b70_2c2b_11ee_be56_0242ac120002);
const RIGHT_COUNTS_UUID: Uuid = Uuid::from_u128(0x0a28672e_2c2b_11ee_be56_0242ac120002);
const WAYPOINT_UUID: Uuid = Uuid::from_u128(0x21e16dea_357a_11ee_be56_0242ac120002);
const POSE_THETA_UUID: Uuid = Uuid::from_u128(0x3cedc40e_3655_11ee_be56_0242ac120002);
const POSE_X_UUID: Uuid = Uuid::from_u128(0xa0c2b3b2_3b1a_11ee_be56_0242ac120002);
const POSE_Y_UUID: Uuid = Uuid::from_u128(0xa0c2b65a_3b1a_11ee_be56_0242ac120002);
const PEN_UUID: Uuid = Uuid::from_u128(0x0daaac7c_3d6a_11ee_be56_0242ac120002);

const BASE_SPEED: f32 = 1.5;
const WHEEL_RADIUS: f32 = 0.045 / 2.0; // meters
const WHEEL_SEPARATION: f32 = 0.105; // meters
const BYTES_ZERO: &[u8; 1] = &[b'0'];
const BYTES_ONE: &[u8; 1] = &[b'1'];

#[derive(PartialEq, Debug)]
enum Mode {
    Manual,
    Auto,
    Debug,
}

#[tokio::main]
async fn main() -> Result<(), Box<dyn Error>> {
    let mode = Mode::Manual;
    println!("Mode: {:?}", mode);

    // TODO: use clap for command line args
    // let args: Vec<String> = env::args().collect();
    // for i in &args {
    //     println!("{i}");
    // }

    // not sure what this part does
    use tracing_subscriber::prelude::*;
    use tracing_subscriber::{fmt, EnvFilter};
    tracing_subscriber::registry()
        .with(fmt::layer())
        .with(
            EnvFilter::builder()
                .with_default_directive(LevelFilter::INFO.into())
                .from_env_lossy(),
        )
        .init();

    // instatiate BLE adapter
    info!("Looking for bluetooth adapter...");
    let adapter = Adapter::default()
        .await
        .ok_or("Bluetooth adapter not found")?;
    adapter.wait_available().await?;

    // find the BLE device service (robot) from the UUID
    let device = adapter
        .discover_devices(&[VANGO_SERVICE_ID])
        .await?
        .next()
        .await
        .ok_or("Failed to discover device")??;
    info!(
        "Found device: {} ({:?})",
        device.name().as_deref().unwrap_or("(unknown)"),
        device.id()
    );
    adapter.connect_device(&device).await?;

    let service = match device
        .discover_services_with_uuid(VANGO_SERVICE_ID)
        .await?
        .get(0)
    {
        Some(service) => service.clone(),
        None => return Err("Service not found".into()),
    };
    info!("Vango service connected");

    // Find and connect to all the characteristics
    let characteristics = service.discover_characteristics().await?;

    let left_speed_chr = characteristics
        .iter()
        .find(|x| x.uuid() == LEFT_SPEED_UUID)
        .ok_or("Left speed characteristic not found")?;

    let right_speed_chr = characteristics
        .iter()
        .find(|x| x.uuid() == RIGHT_SPEED_UUID)
        .ok_or("Right speed characteristic not found")?;

    let pose_x_chr = characteristics
        .iter()
        .find(|x| x.uuid() == POSE_X_UUID)
        .ok_or("Pose x characteristic not found")?;

    let pose_y_chr = characteristics
        .iter()
        .find(|x| x.uuid() == POSE_Y_UUID)
        .ok_or("Pose y characteristic not found")?;

    let pose_theta_chr = characteristics
        .iter()
        .find(|x| x.uuid() == POSE_THETA_UUID)
        .ok_or("Pose theta characteristic not found")?;

    let pen_chr = characteristics
        .iter()
        .find(|x| x.uuid() == PEN_UUID)
        .ok_or("Pen characteristic not found")?;

    info!("Connected all characteristics");

    // Manual mode is remote control mode with the keyboard
    if mode == Mode::Manual {
        let stdin = std::io::stdin();
        let mut stdout = std::io::stdout().into_raw_mode().unwrap();

        let mut speed: f32 = BASE_SPEED.into();
        let mut left_speed: f32 = 0.0;
        let mut right_speed: f32 = 0.0;
        let pose_x_chr1 = pose_x_chr.clone();
        let pose_y_chr1 = pose_y_chr.clone();
        let pose_theta_chr1 = pose_theta_chr.clone();
        let task_handle = tokio::spawn(async move {
            write!(
                stdout,
                "{}{}",
                termion::clear::All,
                termion::cursor::Goto(1, 1),
            )
            .unwrap();
            loop {
                write!(
                    stdout,
                    "{}{}",
                    termion::cursor::Goto(1, 1),
                    termion::clear::CurrentLine
                )
                .unwrap();

                let pose = Pose2D::new(
                    ascii_to_f32(pose_x_chr1.read().await.unwrap()).unwrap(),
                    ascii_to_f32(pose_y_chr1.read().await.unwrap()).unwrap(),
                    ascii_to_f32(pose_theta_chr1.read().await.unwrap()).unwrap(),
                );
                print!("{}\n", pose);

                // tokio::time::sleep(Duration::from_millis(100)).await;
            }
        });

        for c in stdin.keys() {
            match c.unwrap() {
                // Forward
                Key::Char('i') => {
                    // print!("Forward!\r\n");
                    left_speed = speed;
                    right_speed = speed;
                }

                // Backward
                Key::Char(',') => {
                    // print!("Backward!\r\n");
                    left_speed = -speed;
                    right_speed = -speed;
                }

                // Clockwise
                Key::Char('l') => {
                    // print!("Clockwise!\r\n");
                    left_speed = speed;
                    right_speed = -speed;
                }

                // Counter-clockwise
                Key::Char('j') => {
                    // print!("Counter-Clockwise!\r\n");
                    left_speed = -speed;
                    right_speed = speed;
                }

                // Stop
                Key::Char('k') => {
                    // print!("Stop!\r\n");
                    left_speed = 0.0;
                    right_speed = 0.0;
                }

                Key::Char('u') => {
                    pen_chr.write(BYTES_ONE).await.unwrap();
                }
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

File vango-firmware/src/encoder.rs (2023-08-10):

// Code taken from https://github.com/esp-rs/esp-idf-hal/blob/master/examples/pcnt_i64_encoder.rs

#![allow(dead_code)]
use std::cmp::min;
use std::sync::atomic::AtomicI64;
use std::sync::atomic::Ordering;
use std::sync::Arc;

use esp_idf_hal::gpio::AnyInputPin;
use esp_idf_hal::gpio::InputPin;
use esp_idf_hal::pcnt::*;
use esp_idf_hal::peripheral::Peripheral;
use esp_idf_sys::EspError;

use core::f32::consts::PI as pi;

const LOW_LIMIT: i16 = -100;
const HIGH_LIMIT: i16 = 100;

pub const ENCODER_RATE_MS: u64 = 10; // 100 Hz
pub const GEAR_RATIO: u64 = 50;
pub const COUNTS_PER_REV: u64 = 7; // counts per revolution
pub const TICKS_TO_RPS: f32 = 1000.0 / (COUNTS_PER_REV * GEAR_RATIO * ENCODER_RATE_MS * 4) as f32;
pub const TICKS_TO_RPM: f32 =
    60.0 * 1000.0 / (COUNTS_PER_REV * GEAR_RATIO * ENCODER_RATE_MS * 4) as f32;
pub const TICKS_TO_RAD_PER_SEC: f32 =
    pi * 1000.0 / (COUNTS_PER_REV * GEAR_RATIO * ENCODER_RATE_MS * 4) as f32;
pub const TICKS_PER_RAD: f32 = (7.0 * 50.0 * 4.0) / (2.0 * pi);

pub struct Encoder<'d> {
    unit: PcntDriver<'d>,
    approx_value: Arc<AtomicI64>,
}

impl<'d> Encoder<'d> {
    pub fn new<PCNT: Pcnt>(
        pcnt: impl Peripheral<P = PCNT> + 'd,
        pin_a: impl Peripheral<P = impl InputPin> + 'd,
        pin_b: impl Peripheral<P = impl InputPin> + 'd,
    ) -> Result<Self, EspError> {
        let mut unit = PcntDriver::new(
            pcnt,
            Some(pin_a),
            Some(pin_b),
            Option::<AnyInputPin>::None,
            Option::<AnyInputPin>::None,
        )?;
        unit.channel_config(
            PcntChannel::Channel0,
            PinIndex::Pin0,
            PinIndex::Pin1,
            &PcntChannelConfig {
                lctrl_mode: PcntControlMode::Reverse,
                hctrl_mode: PcntControlMode::Keep,
                pos_mode: PcntCountMode::Decrement,
                neg_mode: PcntCountMode::Increment,
                counter_h_lim: HIGH_LIMIT,
                counter_l_lim: LOW_LIMIT,
            },
        )?;
        unit.channel_config(
            PcntChannel::Channel1,
            PinIndex::Pin1,
            PinIndex::Pin0,
            &PcntChannelConfig {
                lctrl_mode: PcntControlMode::Reverse,
                hctrl_mode: PcntControlMode::Keep,
                pos_mode: PcntCountMode::Increment,
                neg_mode: PcntCountMode::Decrement,
                counter_h_lim: HIGH_LIMIT,
                counter_l_lim: LOW_LIMIT,
            },
        )?;

        unit.set_filter_value(min(10 * 80, 1023))?;
        unit.filter_enable()?;

        let approx_value = Arc::new(AtomicI64::new(0));
        // unsafe interrupt code to catch the upper and lower limits from the encoder
        // and track the overflow in `value: Arc<AtomicI64>` - I plan to use this for
        // a wheeled robot's odomerty
        unsafe {
            let approx_value = approx_value.clone();
            unit.subscribe(move |status| {
                let status = PcntEventType::from_repr_truncated(status);
                if status.contains(PcntEvent::HighLimit) {
                    approx_value.fetch_add(HIGH_LIMIT as i64, Ordering::SeqCst);
                }
                if status.contains(PcntEvent::LowLimit) {
                    approx_value.fetch_add(LOW_LIMIT as i64, Ordering::SeqCst);
                }
            })?;
        }
        unit.event_enable(PcntEvent::HighLimit)?;
        unit.event_enable(PcntEvent::LowLimit)?;
        unit.counter_pause()?;
        unit.counter_clear()?;
        unit.counter_resume()?;

        Ok(Self { unit, approx_value })
    }

    pub fn get_value(&self) -> Result<i64, EspError> {
        let value =
            self.approx_value.load(Ordering::Relaxed) + self.unit.get_counter_value()? as i64;
        Ok(value)
    }
}

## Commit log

2023-06-21 control servo with potentiometer
2023-06-23 motor + driver working, not interrupts yet
    - also added num-traits crate and almost_equal in utils.rs
2023-06-23 can read encoder ticks and millis()
2023-06-23 trying to add interrupts again
2023-06-23 interrupt code compiles
    needed to add
    "rustflags = ["-C", "default-linker-libraries"]" to cargo.toml
2023-06-23 interrupt code compiles
    "rustflags = ["-C", "default-linker-libraries"]" to .cargo/config.toml
    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
2023-06-23 sike!, interrupt code does not work
    works in the training repo code but that is with a
    riscv esp32 chip. Building for the standard esp32
    is not working
    [main.rs]
2023-06-24 added flag for interrupt so rpm=0 when not moving
2023-06-24 interrupt based speed control with potentiometer
2023-06-27 motor control with pot again
2023-06-29 both motors with pot working
2023-06-29 basic pid loop and updated gear ratio
2023-06-30 started writing Motor struct
2023-07-03 add encoder.rs back
2023-07-04 RPM looks right with timer interrupt
2023-07-04 PID needs tuning
2023-07-06 fixed map function
    - can't do integer divisions like that...duhh!
    [main.rs]
2023-07-06 added Pen struct
    - creating pwm driver in struct works
    - pen up, down, and get_state methods work
2023-07-06 refactor some of pen.rs, remove motor.rs for now
    need to rewrite motor.rs similar to pen.rs and inlude PID
    controller in there
2023-07-10 add completed PCB, KiCAD project
    note the DRC (rules check) will give a warnings
    on the footprints not matching library symbols.
    This is because I manually changed the GND pads
    in the PCB editor to be square but didn't change
    them in the library
    [500SSP1S1M2REA.step, EG1218.step, XT60PW-M.step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]
2023-07-13 start of the vango desktop client
    [data.csv]
2023-07-14 basic start to the client, add scripts dir
    [data.csv, traj.csv]
2023-07-14 decided I want to track scripts dir
2023-07-15 add wheel radius and separation
2023-07-22 update kicad pcb
    [vango-pcb.kicad_pcb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]
2023-07-22 add servo connector, more space for voltage reg
    [vango-pcb.kicad_pcb, vango-pcb.kicad_sch]
2023-07-22 pcb should be all good now
    [vango-pcb.kicad_pcb, vango-pcb.kicad_sch]
2023-07-22 change text to be "Vango V2"
    [vango-pcb.kicad_pcb]
2023-07-22 add gerber files
    [vango-pcb-B_Cu.gbr, vango-pcb-B_Mask.gbr, vango-pcb-B_Paste.gbr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]
2023-07-23 add ble service
    [partitions.csv]
2023-07-24 ble characteristic for left and right wheel speeds
2023-07-24 move regulator over more, move servo pins
    [vango-pcb-B_Cu.gbr, vango-pcb-B_Mask.gbr, vango-pcb-B_Paste.gbr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]
2023-07-27 interrim commit, may be broken
    [main.rs]
2023-08-03 create vango-utils and replace utils.rs in vango-firmware
    [main.rs]
2023-08-03 replace utils.rs with vango-utils
    [main.rs]
2023-08-09 tuning infrastructure good ish
    - testing setup for tuning works, the PID controller is whack
    - I think the problem is setting the direction
    [data.csv, partitions.csv]
2023-08-10 motor speed control actually works now
    - decided to do much more in the timer ISR
    - using atomic floats now, not sure if thats a bad move but it works
2023-08-10 add speed control results. P control is sufficient it seems
    [speed_kp0.3_ki0_kd0.csv]
2023-08-10 attempted to write motor.rs, gave up
2023-08-11 robot can drive in a circle
    seems to drift a lot. Might be good to average or otherwise
    smooth the speed calculation
    [main.rs]
2023-08-13 Forward working correctly
    revert to here if I break it when trying to do backwards
    [forward_angles.csv]
2023-08-13 MotorDirection enum, holding off on Motor struct etc for now
2023-08-13 backwards works, just need to flip sign of u
    [main.rs]
2023-08-13 seems like some weird overshoot but maybe ok
    [bidirectional_speed.csv]
2023-08-14 speed control works great, maybe a touch of overshoot.
    [bidirectional_speed.csv, speed_control_lpf.csv, speed_kp0.3_ki0_kd0.csv]
2023-08-14 think I like the no-overshoot PD controller better, not too slow
    [forward_angles.csv, p_control.csv, p_speed_control.csv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]
2023-08-15 odometry works! do not normalize angle before using FK
    [odom_results.csv]
2023-08-15 protection for when target speed flips sign
    [main.rs]
2023-08-16 fix direction changing issue
    needed to account for when the target speed was identically zero
    [main.rs]
2023-08-18 almost ready for drawing dev, need to fix pose.theta
    - happy enough with manual control performance for now
    - added servo BLE characteristic and tested it and it works well
    - added flashing neopixel for fun
    [main.rs, pen.rs]
2023-08-21 add neopixel Color enum, docs, remove motor.rs
2023-08-21 added trajectory.rs
    [data.csv, traj.csv]
2023-08-24 PID steering control works but it kinda sucks
    [traj.csv, triangle1.csv]
2023-08-24 rectangle okay
    [rectangle.csv, rectangle2.csv, traj.csv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]
2023-08-25 add oval and donut
    [donut.csv, oval.csv, rectangle.csv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]
